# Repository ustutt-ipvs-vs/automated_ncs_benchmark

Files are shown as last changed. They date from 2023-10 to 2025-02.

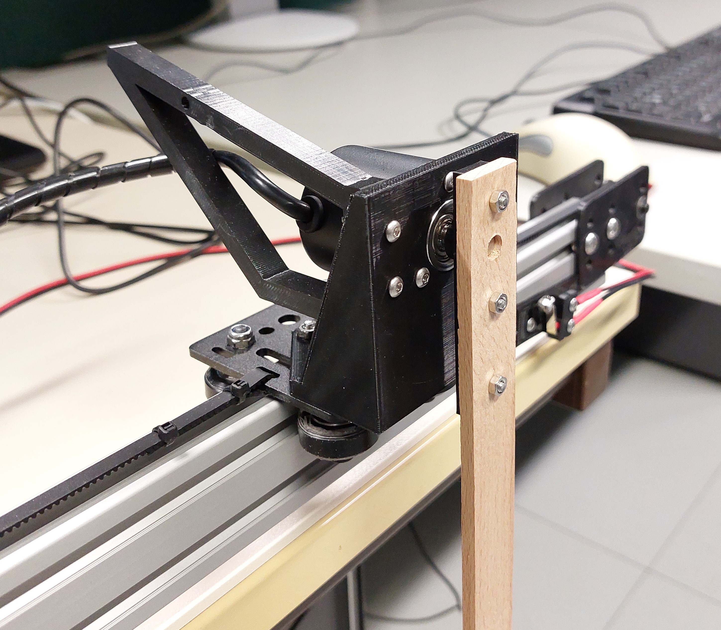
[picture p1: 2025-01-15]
photos/20241224_161821.jpg

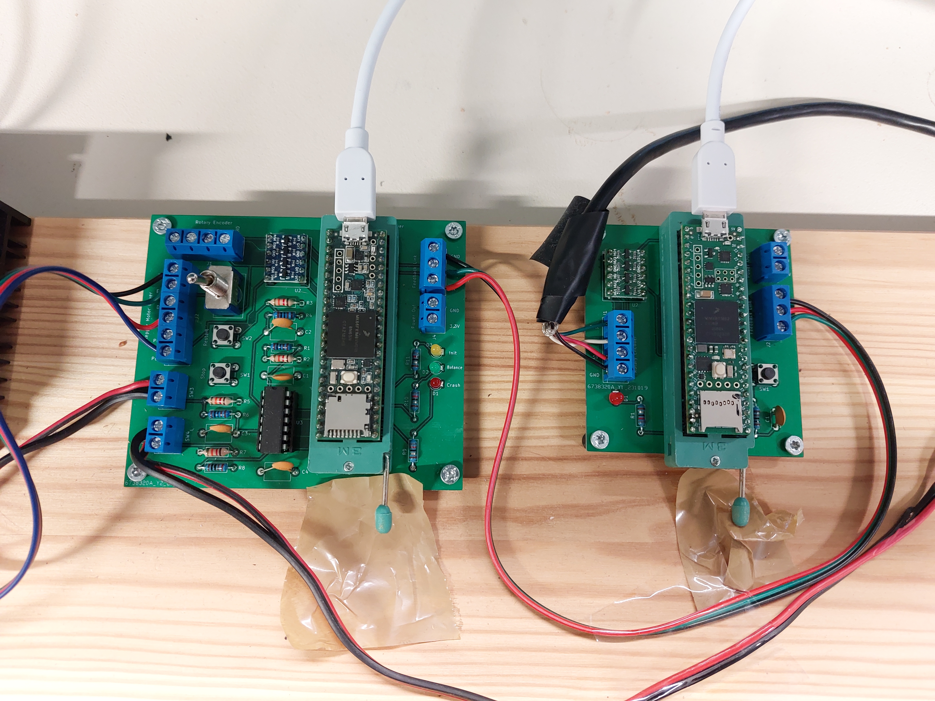
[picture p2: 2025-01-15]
photos/20241224_161937.jpg

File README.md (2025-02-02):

# Automated NCS Benchmark Setup
This repository contains the source code, hardware schematics, 3D printing files, and documentation of the open source benchmark setup described in the paper "Combining Dynamic Deterministic Latency Bounds and Networked Control Systems".

The paper can be found here: https://doi.org/10.1109/IPCCC59868.2024.10850021

The video below shows a demo of an automated evaluation with 15 configurations and re-swing-ups between each configuration.

[Demo Video](https://github.com/ustutt-ipvs-vs/automated_ncs_benchmark/assets/69897594/da2cac4a-8f67-4f81-817d-bd36dadb8c46)

## Overview
This repository is structured as follows:

- `sender-receiver-linux`: Software components for the sender side and receiver side computers
- `sender-receiver-teensy`: Sender and receiver scripts for the Teensy microcontrollers
- `network-config`: Bash scripts to configure the software switch and the endpoints
    - `scheduling-switch-config`: Scripts to configure the Qdisc and queue sizes at the software switch
- `control-approaches-design`: Files containing calculations for the parameters of the various control approaches for the inverted pendulum.
- `PCB-Design`: Design files of the sender and receiver PCB (KiCad)
- `3d-printable-parts`: Design files of the 3D-printed parts that were used for the construction of the inverted pendulum.
- `photos`: Photos of the inverted pendulum

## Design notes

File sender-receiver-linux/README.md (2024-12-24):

# Pendulum Sender and Receiver for Linux
This CMake project contains the code for following programs:
- Sender component for the sensor-side single-board computer
- Receiver component for the actuator-side single-board computer

All the code is written in C++. The following libraries are used:
- `sockpp` to open UDP sockets
- `CppLinuxSerial` to interact with the USB serial interface
- `nlohmann/json` to generate the JSON log files

`sockpp` and `CppLinuxSerial` are shared libraries: They must be installed on the system that is supposed to run the program. They are not included in the executable.
`nlohmann/json` is included in the source code of this project. Thus, the library is included in the executable.

## Preparation
### Installing CMake
Unfortunately, the APT repository only has an outdated version of CMake at the time of writing. Therefore, `sudo apt install cmake` doesn't work.

Instead, install executable from https://cmake.org/download/ .

To use CMake, you need to install `build-essential` too:
```
sudo apt install build-essential
```

### Installing `sockpp`
`sockpp` is a high-level socket library for C++.

```
git clone https://github.com/fpagliughi/sockpp.git
cd sockpp
git checkout f3100f575b38e83a1f2464ca54228bebb1282679
mkdir build
cd build
cmake ..
sudo cmake --build . --target install
```

### Installing `CppLinuxSerial`
`CppLinuxSerial` is a library to access the serial ports in C++.

```
git clone https://github.com/gbmhunter/CppLinuxSerial.git
cd CppLinuxSerial
git checkout ae3c8f7c5e90b3c64e9a3114159923bf45e63e23
mkdir build
cd build
cmake ..
make
sudo make install
```

## Compiling the Source
```
mkdir cmake-build-debug
cd cmake-build-debug
cmake ..
cmake --build .
```

To compile the different targets individually, you can also run instead of the last command:
```
cmake --build . --target pendulum_sender
cmake --build . --target pendulum_receiver
```

## Make Sure Dependencies are Found
You need to make sure that the shared libraries (`sockpp` and `CppLinuxSerial`) can be found. For this purpose, you need to add the path of the libraries (usually `/usr/local/lib`) to the `LD_LIBRARY_PATH` variable:
```
export LD_LIBRARY_PATH=/usr/local/lib:$LD_LIBRARY_PATH
```

## Note About Connecting Teensy via USB
Sometimes, the serial socket doesn't work when the Teensy has been plugged in for a longer time.
In this case, there simply is no input from the serial interface, no errors.

To avoid this problem:
1. Unplug the Teensy
2. Plug in the Teensy
3. Launch the program on the single-board computer immediately (max 10 seconds after plugging in)

## Starting Configurations
The sender and receiver can be started with various parameter options:

### Starting the Sender
#### With single-run config file
````
./pendulum_sender f config_sender_single.json
````

#### With sequence config file
````
./pendulum_sender s config_sender_sequence.json
````

### Starting the Receiver
````
./pendulum_receiver config_receiver.json
````

## Configuration Files
### Sender Config (single run)
```json
{
  "b": 200.0,
  "r": 35.0,
  "numThresholds": 3,
  "thresholds": [0, -200, -400],
  "prioMapping": [0, 1, 2, 7],
  "costs": [1, 1, 1, 0],
  "bias": 0,
  
  /* Option 1: slidingWindow: */
  "sendTriggeringApproach": "slidingWindow",
  "historySize": 100,
  "samplingPeriods": [100, 90, 80, 70, 60, 50, 40, 30, 20, 10],
  "samplingPeriodSensitivityFactor": 1.0,
  "samplingPeriodSensitivityOffset": 0.0,
  
  /* Option 2: simpleThreshold: */
  "sendTriggeringApproach": "simpleThreshold",
  "angleTransmissionThreshold": 1.23,
  
  "initialPriorityClass": 0,
  "serialDeviceName": "auto",
  "receiverAddress": "10.0.1.3",
  "networkDelaysPerPrio": [2, 4, 6, 8, 10, 12, 14, 16]
}
```

with
- `b`: Bucket size of the token bucket
- `r`: Refill rate of the token bucket
- `numThresholds`: Number of thresholds given by the `thresholds` array.
- `thresholds`: Array of thresholds (floating point numbers) for the priority classes. The lowest threhold `- infinity` is ommited from the array.
- `prioMapping`: Array specifying the mapping from the thresholds to the priority classes (integers 0-7).
- `costs`: Array of costs associated with the priority classes. First element associated with best priority class.
- `bias` Bias as an integer value. Is *added* to the raw sensor value before sending it to the receiver. Default value: `0`
- `sendTriggeringApproach`: String. Determines the approach to trigger the sending of a new sensor value. Default: `slidingWindow`. Possible options:
    - `slidingWindow`: Uses a sliding window to determine the maximum absolute angle change. The sampling period is determined by the maximum absolute angle change.
      For this approach, the following parameters are required: `historySize`, `samplingPeriods`, `samplingPeriodSensitivityFactor`, `samplingPeriodSensitivityOffset`.
    - `simpleThreshold`: Uses a simple threshold. Whenever the absolute angle value exceeds the threshold, a new sensor value is sent.
        For this approach, the following parameter is required: `angleTransmissionThreshold`.
- `historySize`: Number of samples kept in the sensor history to determine the maximum absolute angle change.
- `samplingPeriods`: Array of 10 sampling periods in milliseconds, where the first element corresponds to the smallest change and the 10th element corresponds to the largest maximum absolute angle change.
- `initialPriorityClass`: Priority class used at start ()
- `samplingPeriodSensitivityFactor`: Factor by which the maximum absolute angle change is multiplied to determine sampling period. Default value: `1.0`
- `samplingPeriodSensitivityOffset`: Offset by which the maximum absolute angle change is shifted to determine sampling period. Default value: `0.0`
- `serialDeviceName`: Linux file which associated with the serial interface of the sender Teensy. If you set it to `auto`, the computer tries to recognize a Teensy device automatically. Default value: `auto`
- `receiverAddress`: IP address of the receiver PC
- `networkDelaysPerPrio`: Array of network delays in milliseconds (integers) for each priority class. Must have 8 elements. First element associated with the best priority class (0).

### Sender Config (multiple MPTB configurations)
This config allows to run multiple MPTB configurations one after another without manual interaction.
```json
{
  "mptbSequence": [
    {
      "name": "mptb1",
      "durationMinutes": 1.0,
      "b": 200.0,
      "r": 35.0,
      "numThresholds": 3,
      "thresholds": [-20000000, -200, -400],
      "prioMapping": [0, 1, 2, 7],
      "costs": [1, 1, 1, 0]
    },
    {
      "name": "mptb2",
      "durationMinutes": 0.5,
      "b": 5000.0,
      "r": 350.0,
      "numThresholds": 2,
      "thresholds": [-20000, -40000],
      "prioMapping": [0, 1, 2],
      "costs": [2, 1, 0]
    }
  ],

  /* Option 1: slidingWindow: */
  "sendTriggeringApproach": "slidingWindow",
  "historySize": 100,
  "samplingPeriods": [100, 90, 80, 70, 60, 50, 40, 30, 20, 10],
  "samplingPeriodSensitivityFactor": 1.0,
  "samplingPeriodSensitivityOffset": 0.0,

  /* Option 2: simpleThreshold: */
  "sendTriggeringApproach": "simpleThreshold",
  "angleTransmissionThreshold": 1.23,
  
  "bias": 0,
  "serialDeviceName": "auto",
  "receiverAddress": "10.0.1.5",
  "networkDelaysPerPrio": [2, 4, 6, 8, 10, 12, 14, 16]
}

```

with
- `name`: Name of the configuration. This name is used for the file name of the log file.
- `mptbSequence`: Array with an arbitrary number of MPTB configuration objects. These configurations are executed sequentially in the order given by the array.
- `durationMinutes`: Number of minutes (floating point number) that this configuration should be executed.
- All other parameters like in the single-run config.

### Receiver Config
```json
{
  "receiverAddress": "10.0.1.3",
  "pendulumType": "oldPendulum",
  "serialDeviceName": "auto",
  "swingUpBehavior": "crashAndSwingUpAtNewConfig",
  "sailType": "sail14",
  "controllerKVector": [1.0, 2.0, 3.0, 4.0],
  "controllerIntegratorParam": 1.0,
  "controlApproach":"mLQR"
}
```

with 
- `receiverAddress`: IP address of the receiver PC (i.e., own IP address). This IP address is used to bind the UDP socket.
- `pendulumType`: Type of the pendulum. Influences the motor characteristics. Possible options:
    - `oldPendulum`: The pendulum constructed by Ben Carabelli
    - `newPendulum`: The two pendulums constructed by David Augustat
- `serialDeviceName`: Linux file which associated with the serial interface of the receiver Teensy. If you set it to `auto`, the computer tries to recognize a Teensy device automatically. Default value: `auto`
- `swingUpBehavior`: Determines if and when the pendulum should swing up itself. Default: `noSwingUp`. Possible options:
    - `swingUpAtStart`: Only swings up the pendulum at the start. If the pendulum crashes, it will stay crashed.
    - `swingUpAtNewConfigIfCrashed`: Swings up the pendulum at start and at the beginning of each new config, **if the pendulum has crashed before**. If the pendulum is already balancing at the start of a new config, it will not swing up.
    - `crashAndSwingUpAtNewConfig`: Swings up the pendulum at the start. At the beginning of each new config, the pendulum intenionally stops balancing to enforce a crash. Then the pendulum swings up again.
    - `noSwingUp`: Manual mode where the pendulum must be held upwards by the operating person at the beginning. No swing-up.
- `sailType`: Determines which sail is used. Default: `noSail`. Possible options:
    - `noSail`: No sail is used.
    - `sail10`
    - `sail14`
    - `sail17`
    - `sail20`
- `controllerKVector`: Vector of 4 floating point numbers. The RobustIO controller uses this vector as the K vector. Default: `[3.6723, 13.5022, -74.6153, -19.8637]`
- `controllerIntegratorParam`: Floating point number. The RobustIO controller uses this value as the integrator parameter. Default: `5.0322`
- `controlApproach`: String. Determines which control approach is used. Default: `mLQR`. Possible options:
    - `mLQR`
    - `RobustIO`

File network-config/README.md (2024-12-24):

# Network Configuration Scripts for VLANs:

## Scripts:
Run the scripts on the devices respectively to set up the correct network config.

`configure-switch.sh` does the following
- Sets up VLANs on `enp1s0f0`, `enp1s0f1` `enp1s0f2` and `enp1s0f3` with VLAN ID `100`. For this purpose, the VLAN interfaces `enp1s0f0.100`, `enp1s0f1.100`, `enp1s0f2.100` and `enp1s0f3.100` get created.
- Creates a virtual bridge between `enp1s0f0.100`, `enp1s0f1.100`, `enp1s0f2.100` and `enp1s0f3.100`.
- Assigns the IP address to the switch PC.

All other `configure-*.sh` scripts set up a VLAN interface set up VLANs as `eth0.100` or `enp0s25.100` interfaces with VLAN ID 100 and assign an IP address.

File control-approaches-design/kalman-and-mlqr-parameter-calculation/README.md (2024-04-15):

# How to use
Make sure that the [Julia programming language](https://julialang.org/) is installed on your machine.

Then run from this directory:
```
julia demonstrator-multi-period.jl
```

The script creates a header file 
```
../sender-receiver-teensy/pendulum_receiver1/KalmanAndMLQRParameters.h
```
with the parameters for the Kalman filter and the mLQR controller.

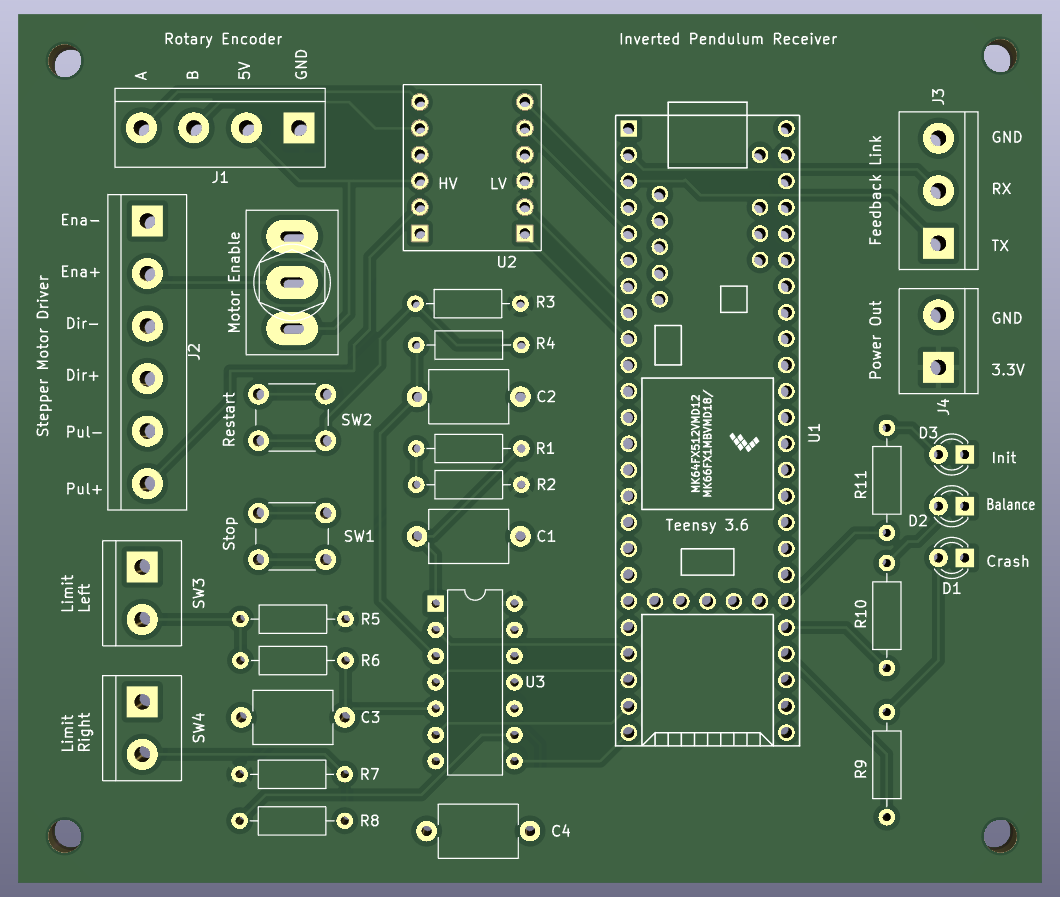
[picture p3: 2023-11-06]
PCB-Design/PCB-Images/receiver-front_06-10-2023.png

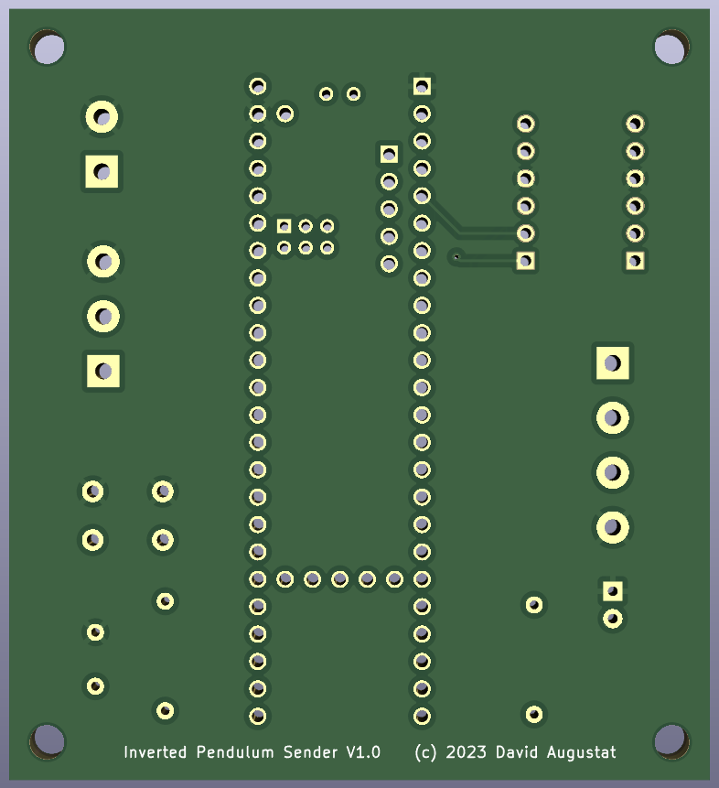
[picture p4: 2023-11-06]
PCB-Design/PCB-Images/sender-back_06-10-2023.png

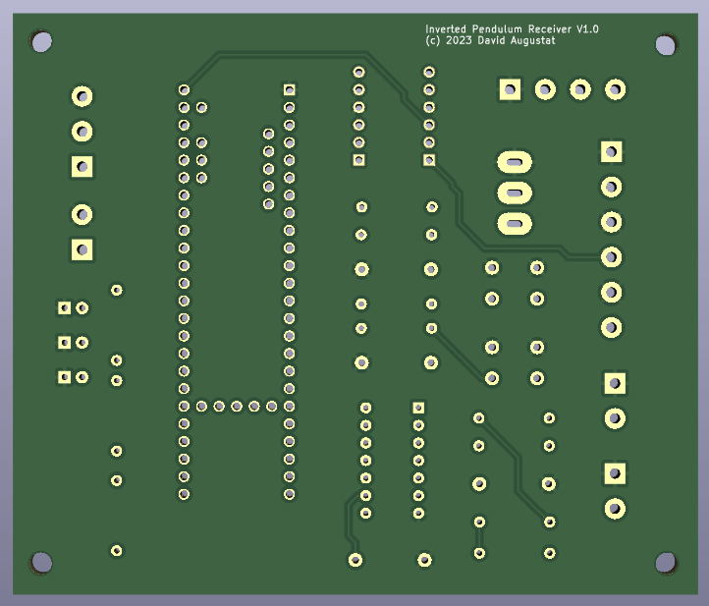
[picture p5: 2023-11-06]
PCB-Design/PCB-Images/receiver-back_06-10-2023.png

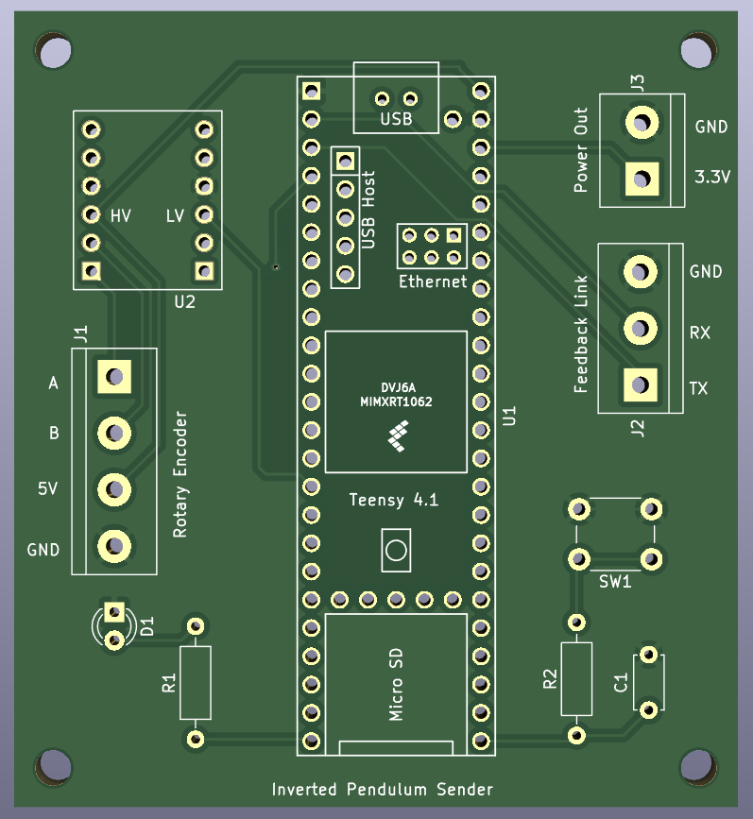
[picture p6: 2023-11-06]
PCB-Design/PCB-Images/sender-front_06-10-2023.png

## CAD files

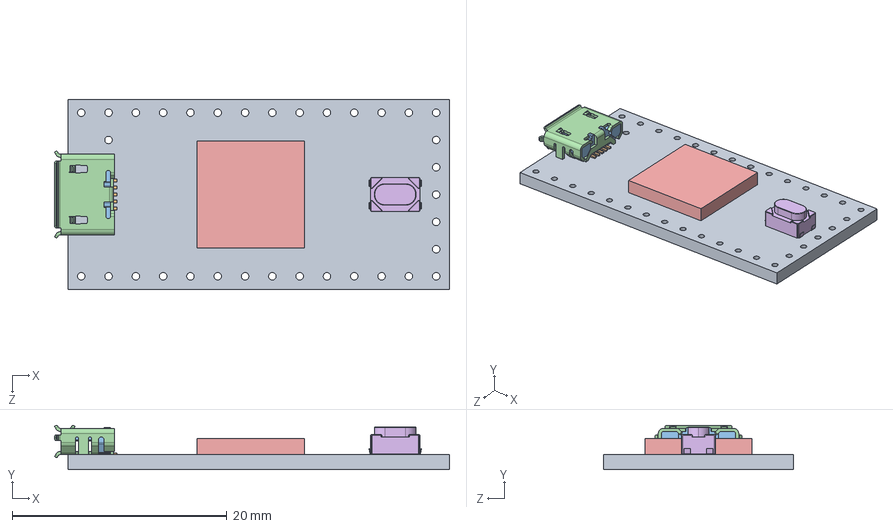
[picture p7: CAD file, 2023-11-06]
PCB-Design/Symbols/teensy.pretty-master/Teensy_4.0_Assembly.STEP
36.8 x 4.12 x 17.7 mm
Teensy_4.0_PCB
Micro USB-B Female 5Pin SMD
NXP iMXRT1062
SKRPACE010 v4

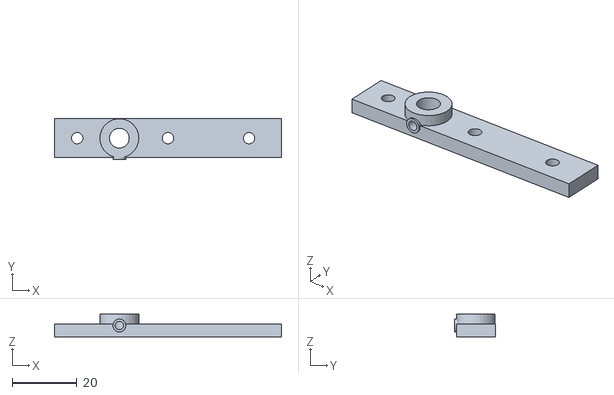
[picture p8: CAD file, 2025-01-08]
3d-printable-parts/rod_attachment.stl
70.0 x 12.5 x 7.00

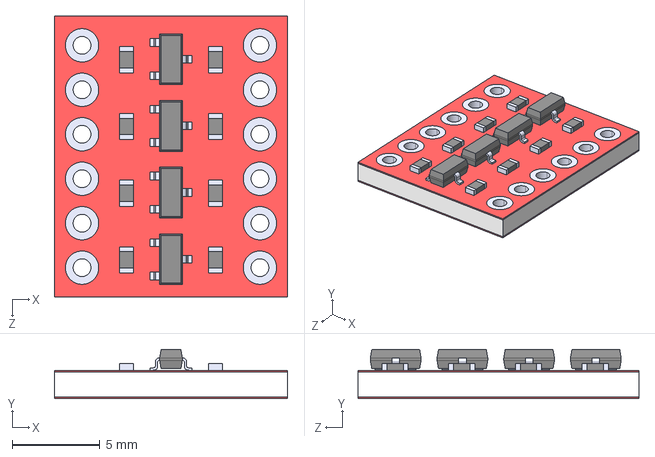
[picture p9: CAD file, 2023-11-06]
PCB-Design/Symbols/BOB-12009/BOB-12009.step
13.3 x 2.80 x 16.1 mm

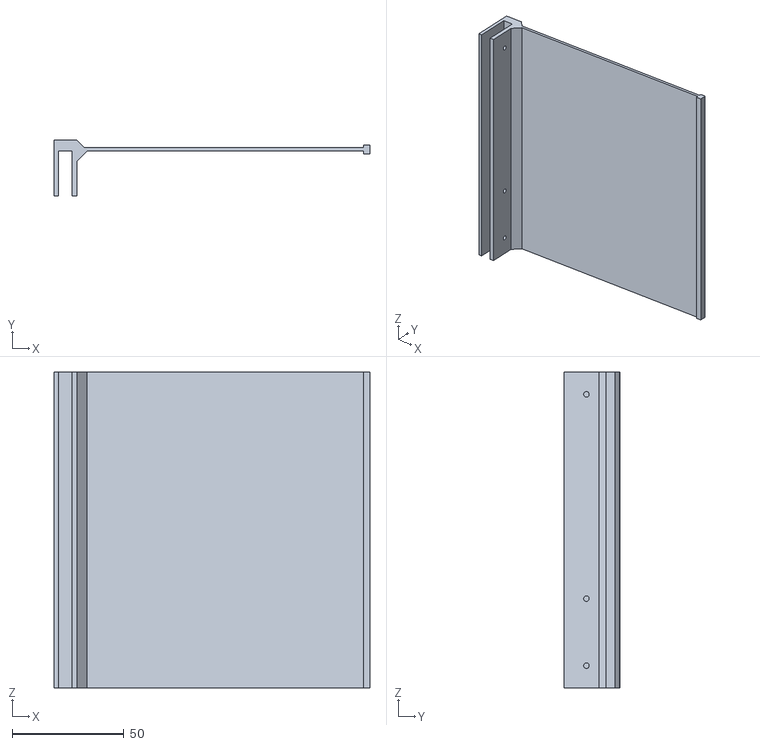
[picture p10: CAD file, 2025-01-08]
3d-printable-parts/sail_14x14.stl
141.4 x 25.0 x 141.4

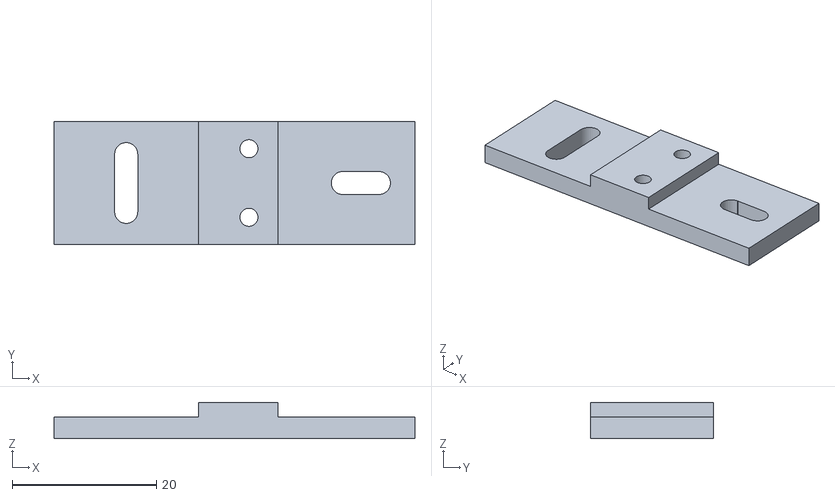
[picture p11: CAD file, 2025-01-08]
3d-printable-parts/endstop_mount.stl
50.0 x 17.0 x 5.00

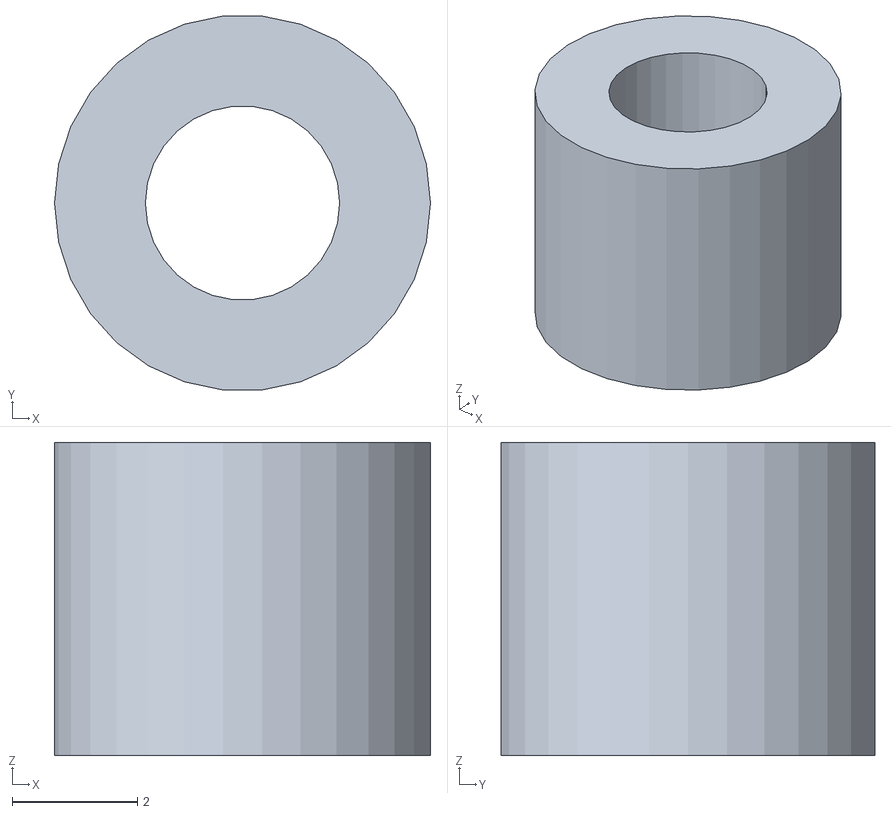
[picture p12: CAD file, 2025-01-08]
3d-printable-parts/pcb_distance.stl
6.00 x 5.97 x 5.00

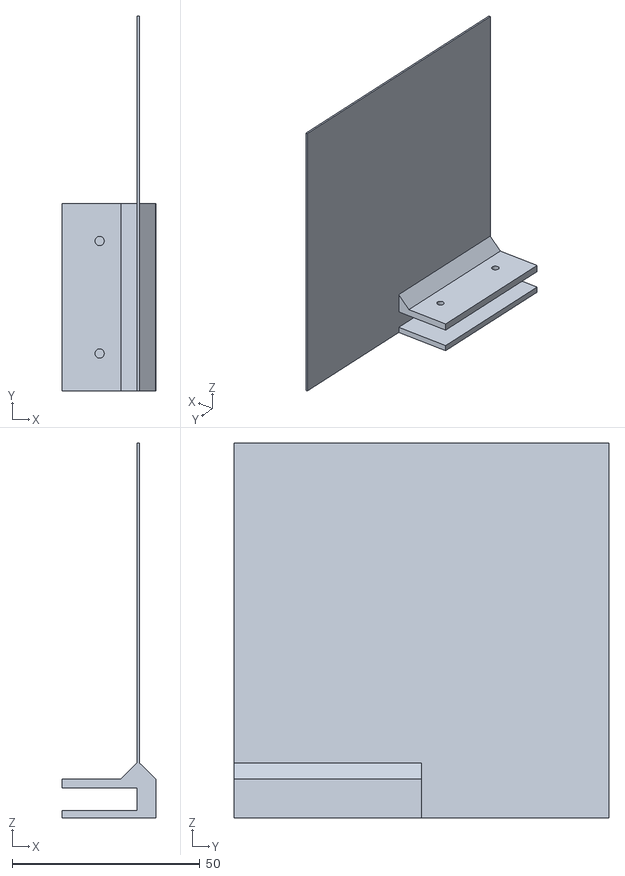
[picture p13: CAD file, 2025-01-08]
3d-printable-parts/sail_10x10.stl
25.0 x 100.0 x 100.0

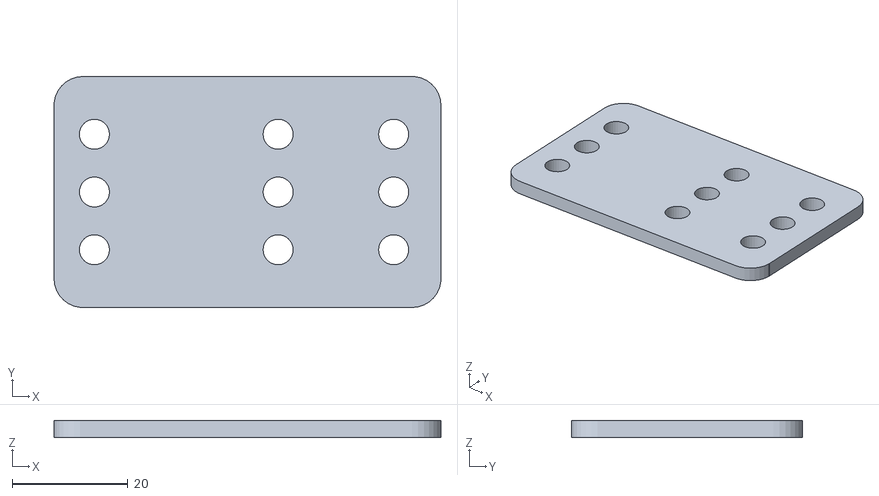
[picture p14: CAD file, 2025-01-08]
3d-printable-parts/idler_mount.stl
67.0 x 40.0 x 3.00

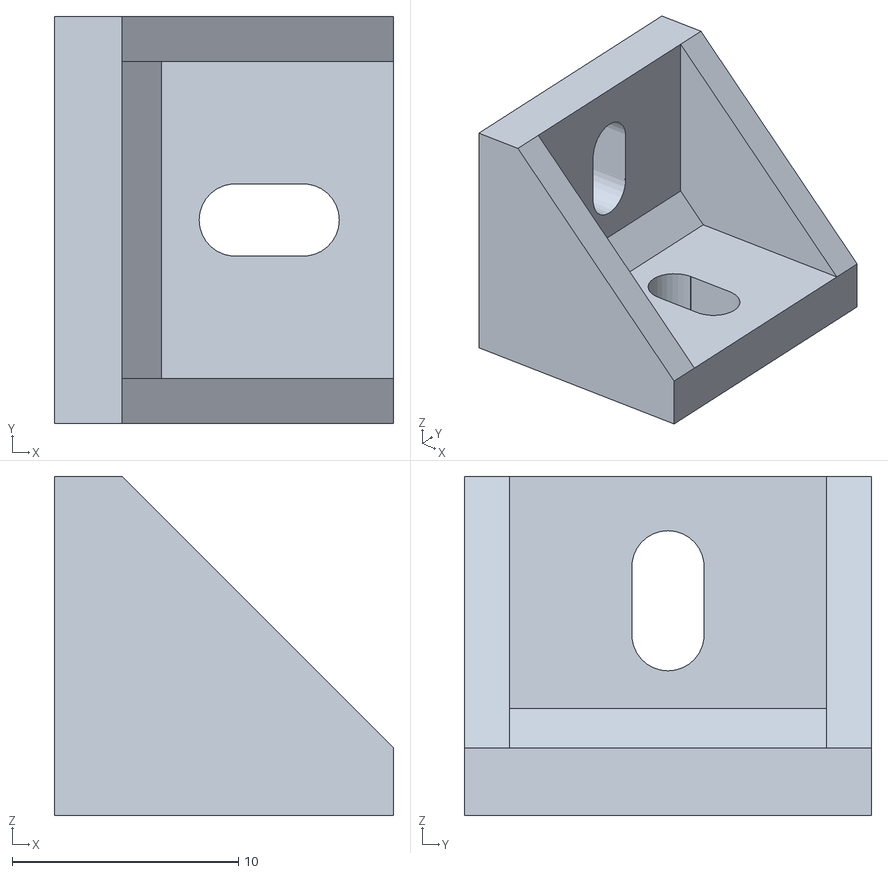
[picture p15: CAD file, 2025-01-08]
3d-printable-parts/corner_profile_mount.stl
15.0 x 18.0 x 15.0

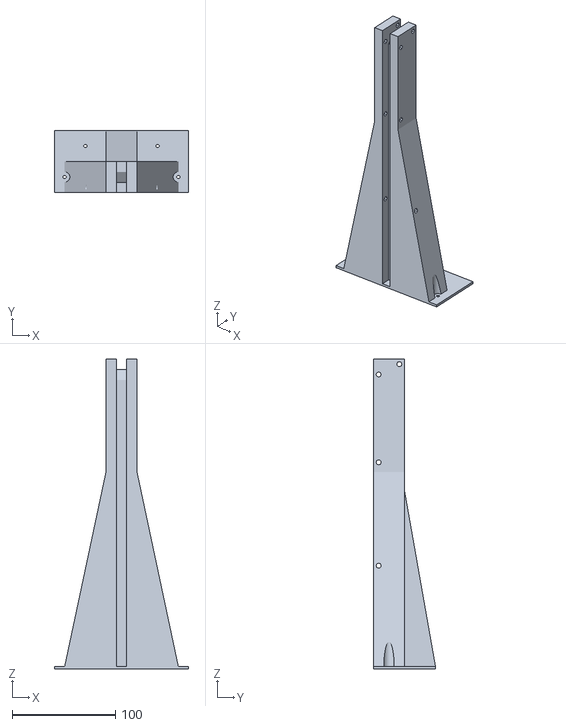
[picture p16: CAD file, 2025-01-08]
3d-printable-parts/cable_tower.stl
130.0 x 60.0 x 300.0

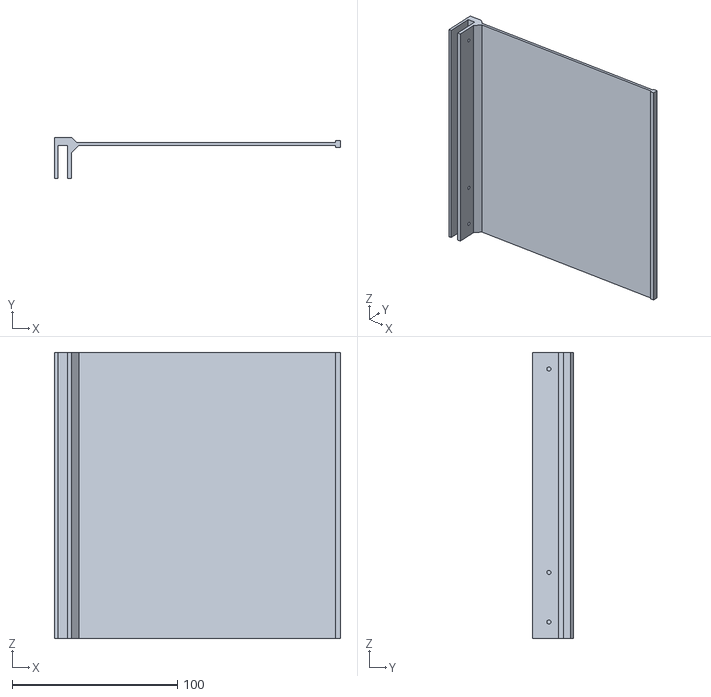
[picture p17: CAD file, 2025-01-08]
3d-printable-parts/sail_17x17.stl
173.2 x 25.0 x 173.2

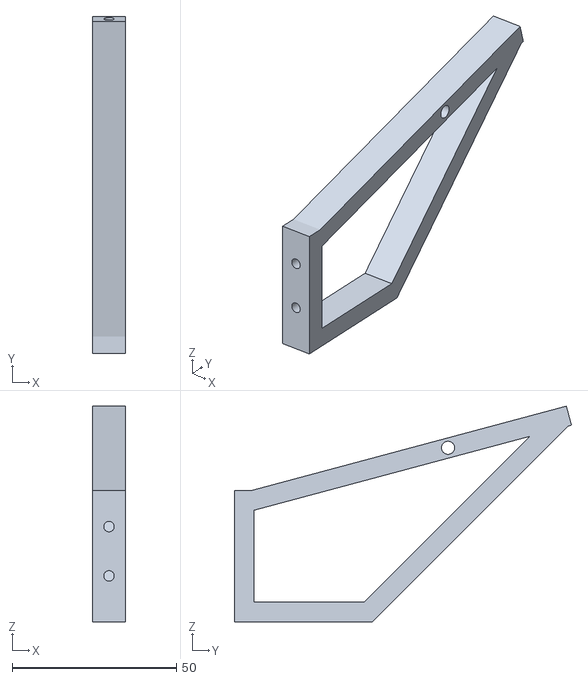
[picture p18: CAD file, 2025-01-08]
3d-printable-parts/sensor_mount_cable_guide.stl
10.0 x 102.6 x 65.7

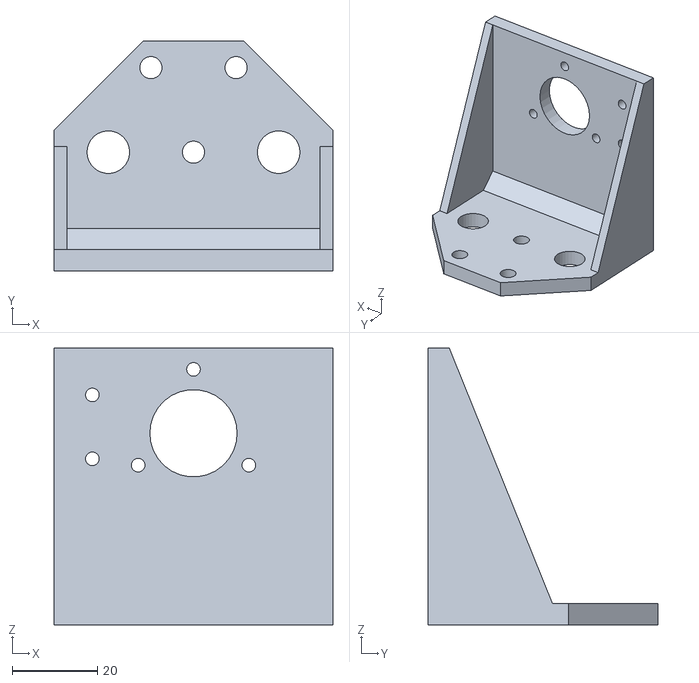
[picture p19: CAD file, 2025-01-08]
3d-printable-parts/sensor_mount.stl
65.5 x 54.0 x 65.0

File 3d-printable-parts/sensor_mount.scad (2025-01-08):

$fn=30;

width=39+15;
length=65.5;
height=65;
screw_d=3.2;

sensor_mount();
translate([4,6,height-6]) sensor_cable_guide();


module sensor_cable_guide(){
    guide_length = 100; // Changing this value is not fully supported
    difference(){
        union(){
            translate([0,6,0]) rotate([15,0,0]) cube([10,guide_length,6]);
            translate([0,0,-34]) cube([10,6,40]);
            translate([0,0,-34]) cube([10,guide_length-64+6,6]);
            translate([0,6+guide_length-64,-34]) rotate([45,0,0]) cube([10,85,6]);
        }
        
        // Screwholes + nuts
        translate([5,-0.1,-20]) rotate([-90,0,0]) cylinder(h=10,d=screw_d);
        translate([5,4,-20]) rotate([-90,0,0]) cylinder(h = 4, r=3.2, $fn=6);
        translate([5,-0.1,-5]) rotate([-90,0,0]) cylinder(h=10,d=screw_d);
        translate([5,4,-5]) rotate([-90,0,0]) cylinder(h = 4, r=3.2, $fn=6); 
    
        
        // Filament hole
        translate([5,70,20]) rotate([-75,0,0]) cylinder(h=50,d=3.2);
        
        // Ziptie hole
        translate([-0.1,65,19.]) rotate([0,90,0]) cylinder(h=12,d=4);
           
    }
    
}
module sensor_mount(){
    difference(){
        union(){
            cube([length,width,5]);
            cube([length,5,height]);
            
            translate([0,10,5]) rotate([135,0,0]) cube([length,10,4]);
            
            // Stability sides
            translate([0,5,height]) rotate([22-180,0,0]) cube([3,25,height+10]);
            translate([length-3,5,height]) rotate([22-180,0,0]) cube([3,25,height+10]);
        }
    
        // Sensor Hole
        translate([length/2,-0.1,45]) rotate([-90,0,0]) cylinder(h=10,d=20.5);
        
        // Sensor Screw holes
        translate([length/2,-0.1,45+15]) rotate([-90,0,0]) cylinder(h=10,d=3.2);
        translate([length/2+12.99,-0.1,45-7.5]) rotate([-90,0,0]) cylinder(h=10,d=3.2);
        translate([length/2-12.99,-0.1,45-7.5]) rotate([-90,0,0]) cylinder(h=10,d=3.2);
        
        // Cable guide holes
        translate([9,-0.1,39]) rotate([-90,0,0]) cylinder(h=10,d=3.2);
        translate([9,-0.1,39+15]) rotate([-90,0,0]) cylinder(h=10,d=3.2);
        
    
        translate([0,15,0]){
        // Screwholes bottom
        translate([32.75,12.9,-0.1]) cylinder(h=10,d=5.2);
        translate([22.75,32.75,-0.1]) cylinder(h=10,d=5.2);      
        translate([42.75,32.75,-0.1]) cylinder(h=10,d=5.2);
        
        // Screwheads bottom
        translate([32.75,12.9,5]) cylinder(h=10,d=11);

        // Wheel Nut openings
        translate([12.75,12.9,-0.1]) cylinder(h=10,d=10);
        translate([length-12.75,12.9,-0.1]) cylinder(h=10,d=10);
            
        // 45° Cut bottom
        translate([0,18,-0.1]) rotate([0,0,45]) cube([30,20,6]);
        translate([length,18,-0.1]) rotate([0,0,45]) cube([20,30,6]);
            
        }

        
        //bottom and back cut
        translate([-0.1,-0.1,-length]) cube([length+1,width+1,length]);
        translate([-0.1,-length,-length]) cube([length+1,length,2*length]);
    
    }  
}

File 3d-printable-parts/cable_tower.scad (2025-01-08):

height=300;
plate_thick = 2.5;
screw_d=3.2;

cable_tower();


module cable_tower(){
    difference(){
        union(){
            cube([30,30,height]);
            translate([-10,0,0]) cube([50,30,50]);
            translate([-50,0,0]) cube([130,60,plate_thick]);
            
            translate([-40,0,plate_thick]) rotate([0,12,0]) cube([30,30,195]);
            translate([40+30,30,plate_thick]) rotate([0,12,180]) cube([30,30,195]);
            translate([0,60,plate_thick]) rotate([0,10,270]) cube([30,30,175]);
                      
        }
    
    // Bottom cut
    translate([-50,-10,-20]) cube([130,80,20]);
        
    // Cable channel
    translate([10,-0.1,plate_thick]) cube([10,10,height]);
    translate([10,0,height-10]) cube([10,31,11]);
    translate([10,0,height-30]) rotate([45,0,0]) cube([10,31,11]);
        
    // Ziptie holes
    translate([-10,5,height-15]) rotate([0,90,0]) cylinder(h=50,d=5);
    translate([-10,25,height-5]) rotate([0,90,0]) cylinder(h=50,d=5);
    translate([-10,5,height-100]) rotate([0,90,0]) cylinder(h=50,d=5);
    translate([-100,5,height-200]) rotate([0,90,0]) cylinder(h=200,d=5);
    
    // Screwholes bottom
    translate([-40,15,-0.1]) cylinder(h=5, d=screw_d, $fn=30);
    translate([70,15,-0.1]) cylinder(h=5, d=screw_d, $fn=30);
    translate([-40,15,plate_thick]) cylinder(h=25, d=10, $fn=30);
    translate([70,15,plate_thick]) cylinder(h=25, d=10, $fn=30);
    
    translate([-20,45,-0.1]) cylinder(h=5, d=screw_d, $fn=30);
    translate([50,45,-0.1]) cylinder(h=5, d=screw_d, $fn=30);
    
        
    
    }  
}

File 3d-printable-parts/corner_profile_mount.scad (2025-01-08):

width=18;
length=15;
screw_d=3.2;

corner();


module corner(){
    difference(){
        union(){
            cube([length,width,3]);
            cube([3,width,length]);
            
            translate([0,0,3.5]) rotate([0,45,0]) cube([4,width,3]);
            translate([3,0,length]) rotate([0,135,0]) cube([length-3,2,sqrt(2*(length-3)*(length-3))]);
            translate([3,width-2,length]) rotate([0,135,0]) cube([length-3,2,sqrt(2*(length-3)*(length-3))]);
        }
    
    
    // Screwholes bottom
    translate([length-7,width/2-screw_d/2,-0.1]) cube([3,screw_d,5]);
    translate([length-7,width/2,-0.1]) cylinder(h=5, d=screw_d, $fn=30);
    translate([length-4,width/2,-0.1]) cylinder(h=5, d=screw_d, $fn=30);
    
    // Screwholes side
    translate([-0.1,width/2-screw_d/2,length-7]) cube([5,screw_d,3]);
    translate([-0.1,width/2,length-7]) rotate([0,90,0]) cylinder(h=5, d=screw_d, $fn=30);
    translate([-0.1,width/2,length-4]) rotate([0,90,0]) cylinder(h=5, d=screw_d, $fn=30);
        
    //bottom and back cut
    translate([-0.1,-0.1,-length]) cube([length,width+1,length]);
    translate([-length,-0.1,-0.1]) cube([length,width+1,length+1]);
    
    }  
}

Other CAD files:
3d-printable-parts/endstop_mount.scad
3d-printable-parts/idler_mount.scad
3d-printable-parts/pcb_distance.scad
3d-printable-parts/rod_attachment.scad
3d-printable-parts/sail.scad

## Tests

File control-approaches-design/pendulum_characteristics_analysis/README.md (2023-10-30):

# How To

1. Upload the `teensy_encoder_serial_readout.ino` sketch onto a Teensy microcontroller that is connected to a rotary encoder on pin 2 an 3.
2. Plug in the Teensy in the computer. The teensy immediately starts writing the raw encoder values to the Serial interface every millisecond.
3. Run the `teensy_encoder_log.sh` script to receive the values from the serial interface and write them to a log file.
4. Do your measurements.
5. Stop the script with `Ctrl+C` when you are done measuring.
6. Use the `analyze_trace.py` script to analyze the created log file.

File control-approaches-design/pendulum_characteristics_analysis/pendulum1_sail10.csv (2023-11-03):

timeMicros | encoderValue
467001 | 0
468001 | 0
469001 | 0
470001 | 0
1099000 | 0
1100000 | 0
1101000 | 0
1102000 | 0
1103000 | 0
1104000 | 0
1105000 | 0
1106000 | 0
1107000 | 0
1108000 | 0
1109000 | 0
1110000 | 0
1111000 | 0
1112000 | 0
1113000 | 0
1114000 | 0
1115000 | 0
1116000 | 0
1117000 | 0
1118000 | 0
1119000 | 0
1120000 | 0
1121000 | 0
1122000 | 0
1123000 | 0
1124000 | 0
1125000 | 0
1126000 | 0
1127000 | 0
1128000 | 0
1129000 | 0
1130000 | 0
1131000 | 0
1132000 | 0
1133000 | 0
1134000 | 0
1135000 | 0
1136000 | 0
1137000 | 0
1138000 | 0
1139000 | 0
1140000 | 0
1141000 | 0
1142000 | 0
1143000 | 0
1144000 | 0
1145000 | 0
1146000 | 0
1147000 | 0
1148000 | 0
1149000 | 0
1150000 | 0
1151000 | 0
1152000 | 0
1153000 | 0
1154000 | 0
1155000 | 0
1156000 | 0
1157000 | 0
1158000 | 0
1159000 | 0
1160000 | 0
1161000 | 0
1162000 | 0
1163000 | 0
1164000 | 0
1165000 | 0
1166000 | 0
1167000 | 0
1168000 | 0
1169000 | 0
1170000 | 0
1171000 | 0
1172000 | 0
1173000 | 0
1174000 | 0
1175000 | 0
1176000 | 0
1177000 | 0
1178000 | 0
1179000 | 0
1180000 | 0
1181000 | 0
1182000 | 0
1183000 | 0
1184000 | 0
1185000 | 0
1186000 | 0
1187000 | 0
1188000 | 0
1189000 | 0
1190000 | 0
1191000 | 0
1192000 | 0
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

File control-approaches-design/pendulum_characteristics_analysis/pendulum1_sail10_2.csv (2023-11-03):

timeMicros | encoderValue
508001 | 0
509001 | 0
510001 | 0
511001 | 0
956002 | 0
957002 | 0
958002 | 0
959002 | 0
960002 | 0
961002 | 0
962002 | 0
963002 | 0
964002 | 0
965002 | 0
966002 | 0
967002 | 0
968002 | 0
969002 | 0
970002 | 0
971002 | 0
972002 | 0
973002 | 0
974002 | 0
975002 | 0
976002 | 0
977002 | 0
978002 | 0
979002 | 0
980002 | 0
981002 | 0
982002 | 0
983002 | 0
984002 | 0
985002 | 0
986002 | 0
987002 | 0
988002 | 0
989002 | 0
990002 | 0
991002 | 0
992002 | 0
993002 | 0
994002 | 0
995002 | 0
996002 | 0
997002 | 0
998002 | 0
999002 | 0
1000002 | 0
1001002 | 0
1002002 | 0
1003002 | 0
1004002 | 0
1005002 | 0
1006002 | 0
1007002 | 0
1008002 | 0
1009002 | 0
1010002 | 0
1011002 | 0
1012002 | 0
1013002 | 0
1014002 | 0
1015002 | 0
1016002 | 0
1017002 | 0
1018002 | 0
1019002 | 0
1020002 | 0
1021002 | 0
1022002 | 0
1023002 | 0
1024002 | 0
1025002 | 0
1026002 | 0
1027002 | 0
1028002 | 0
1029002 | 0
1030002 | 0
1031002 | 0
1032002 | 0
1033002 | 0
1034002 | 0
1035002 | 0
1036002 | 0
1037002 | 0
1038002 | 0
1039002 | 0
1040002 | 0
1041002 | 0
1042002 | 0
1043002 | 0
1044002 | 0
1045002 | 0
1046002 | 0
1047002 | 0
1048002 | 0
1049002 | 0
1050002 | 0
1051002 | 0
1052002 | 0
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

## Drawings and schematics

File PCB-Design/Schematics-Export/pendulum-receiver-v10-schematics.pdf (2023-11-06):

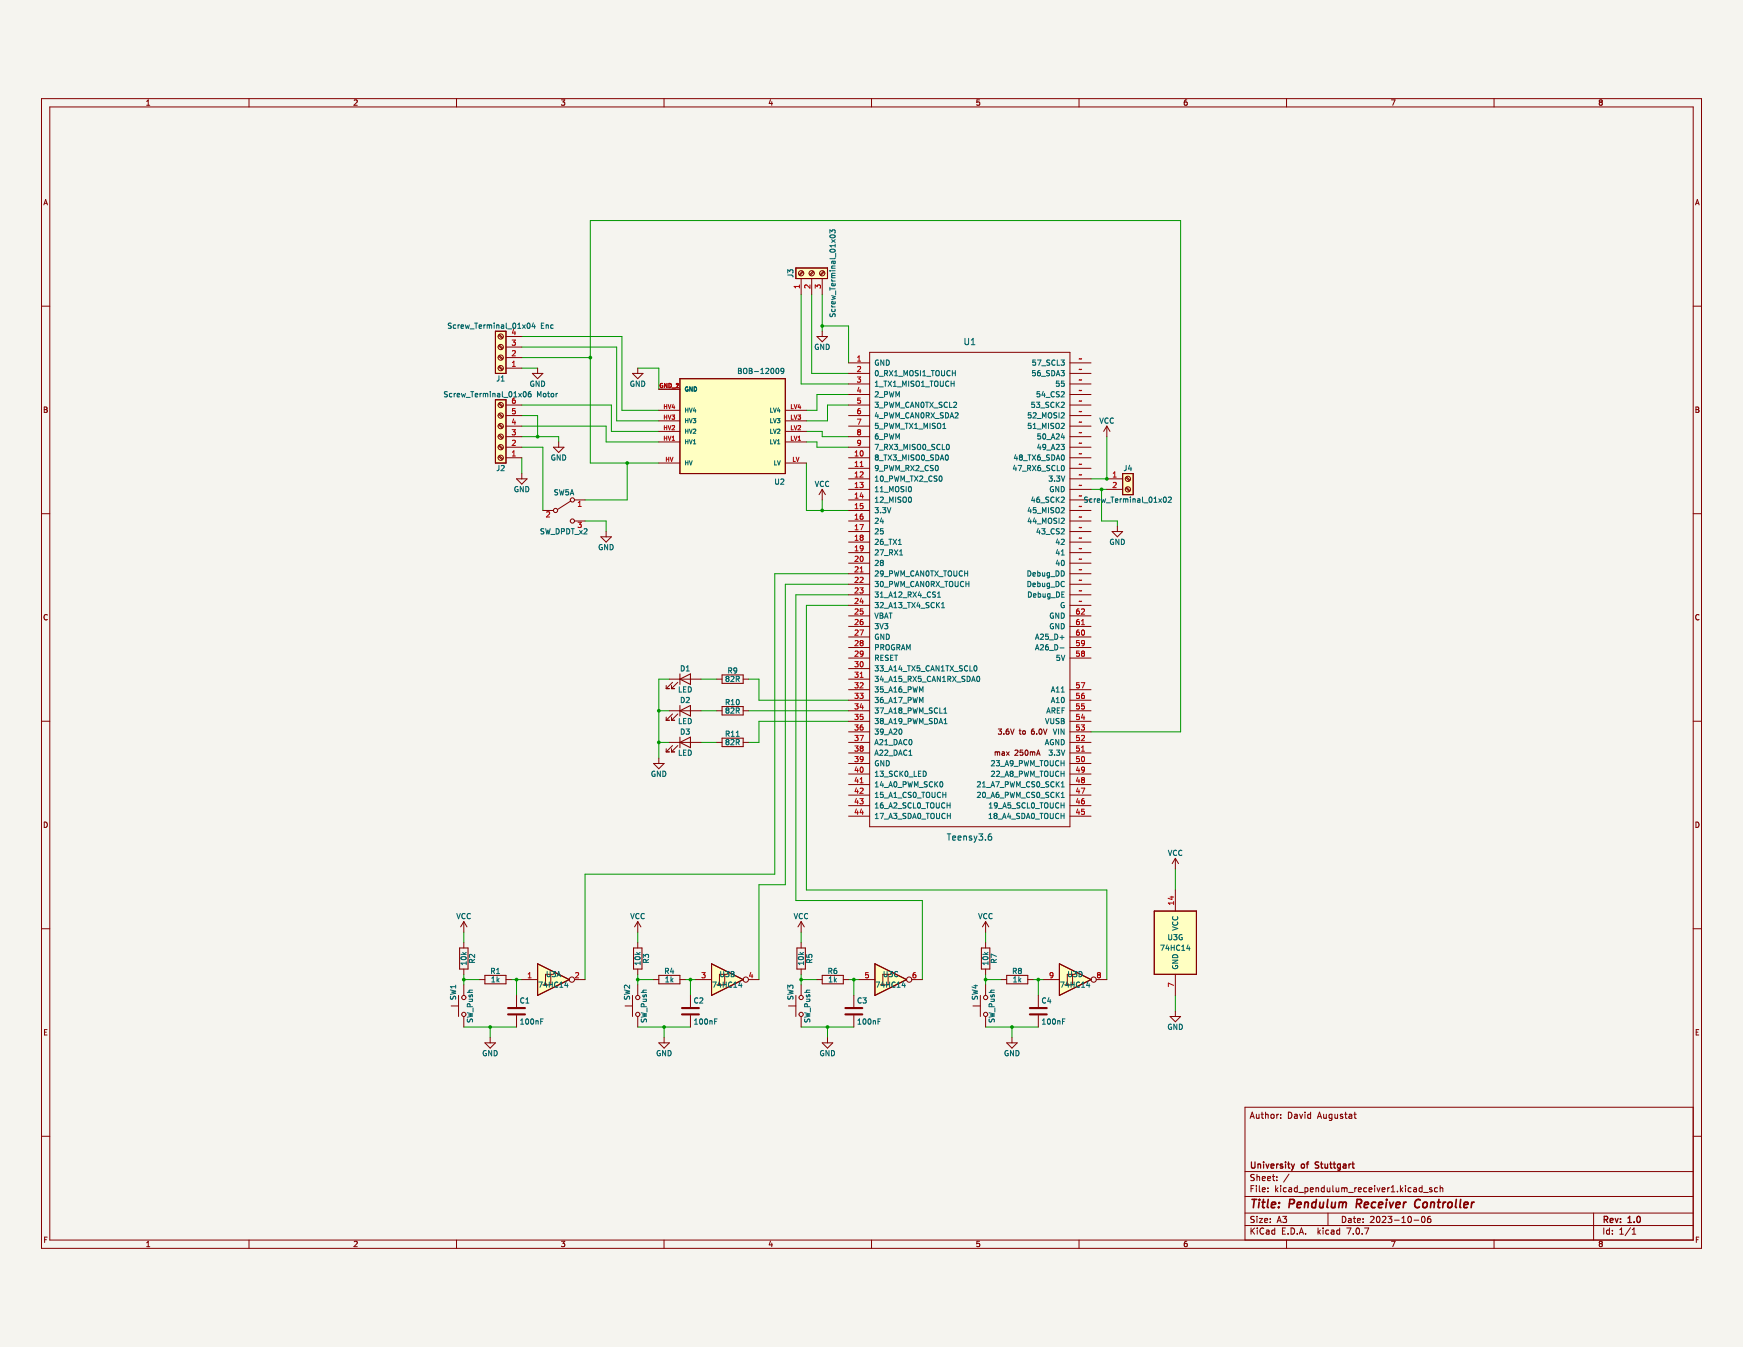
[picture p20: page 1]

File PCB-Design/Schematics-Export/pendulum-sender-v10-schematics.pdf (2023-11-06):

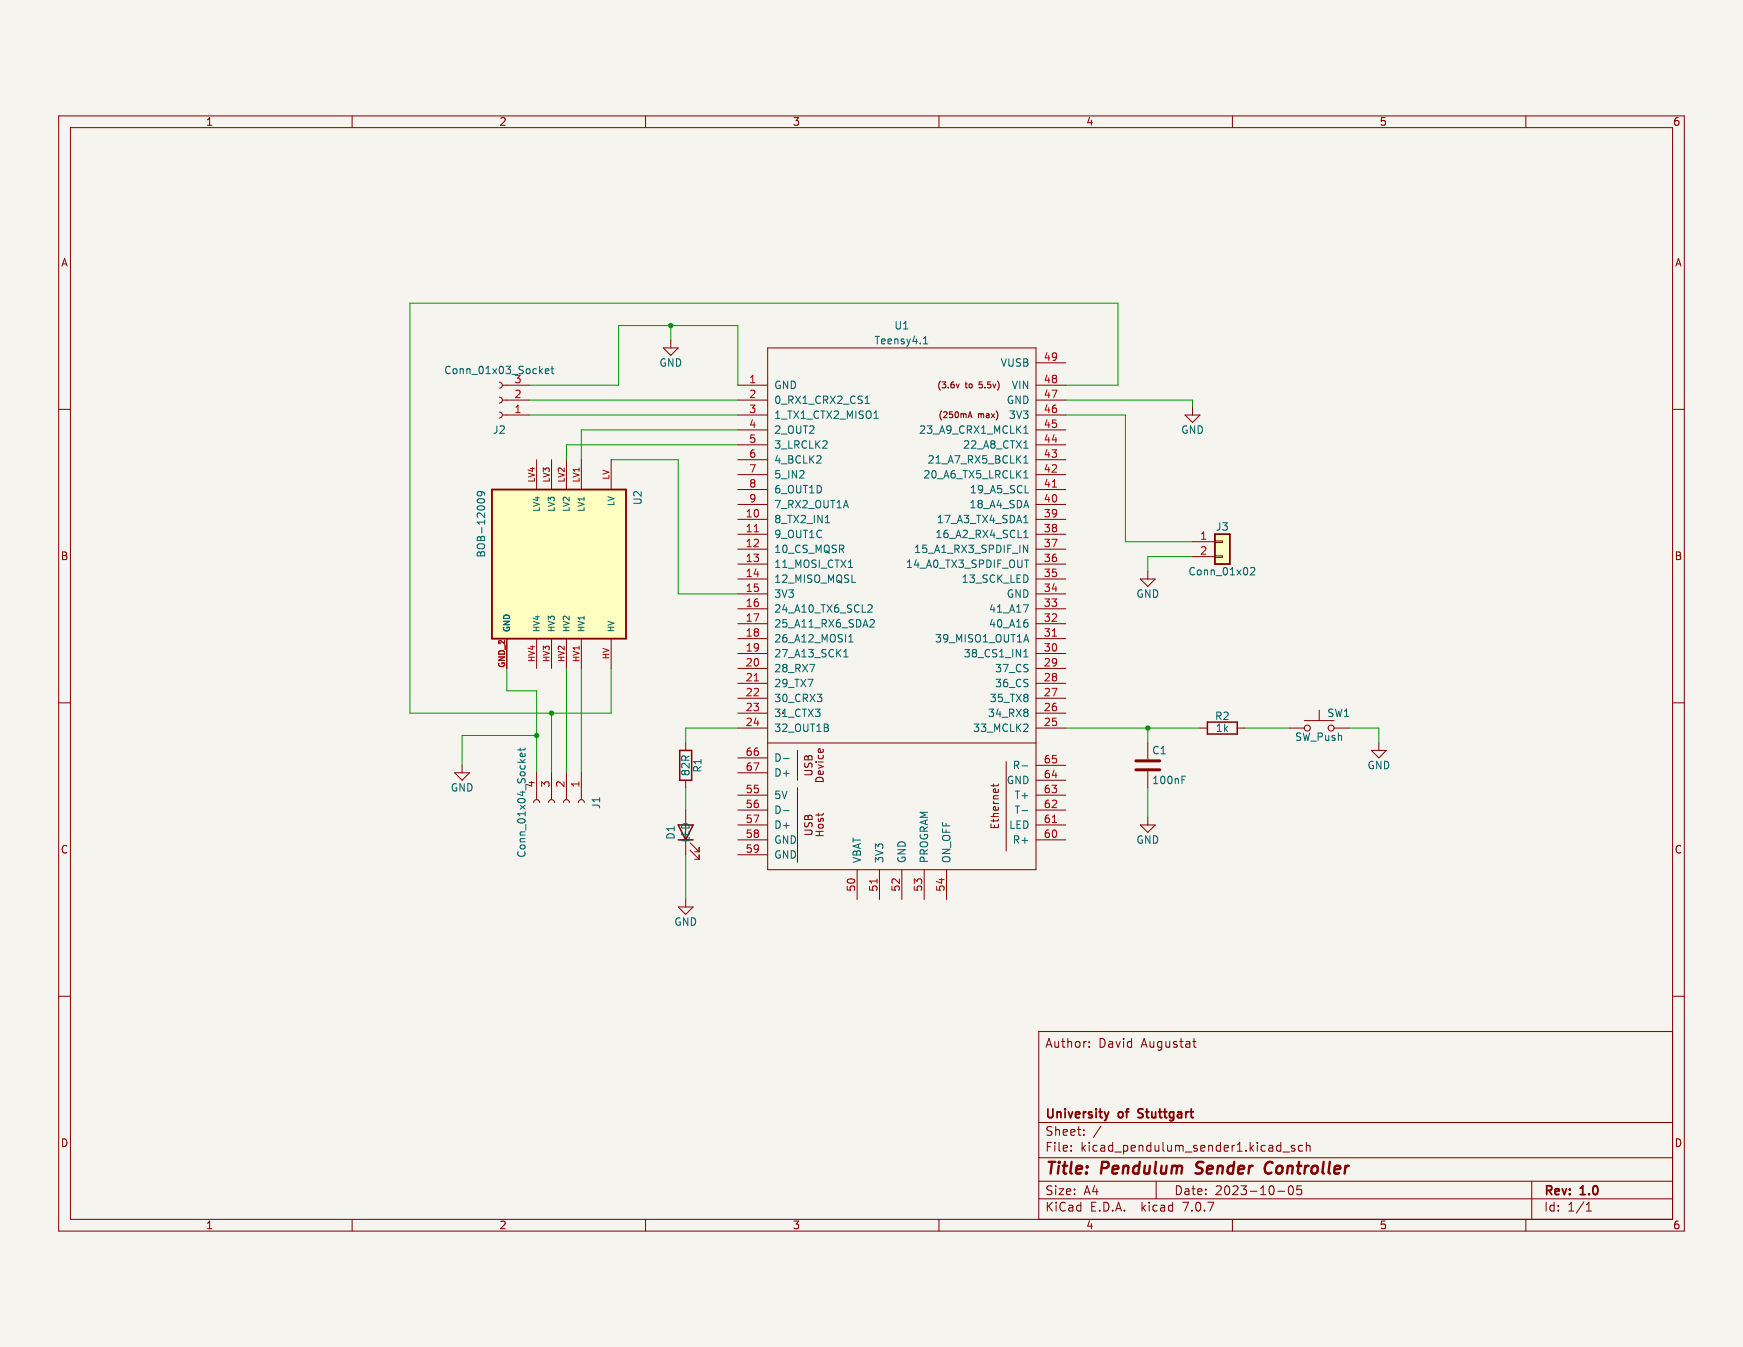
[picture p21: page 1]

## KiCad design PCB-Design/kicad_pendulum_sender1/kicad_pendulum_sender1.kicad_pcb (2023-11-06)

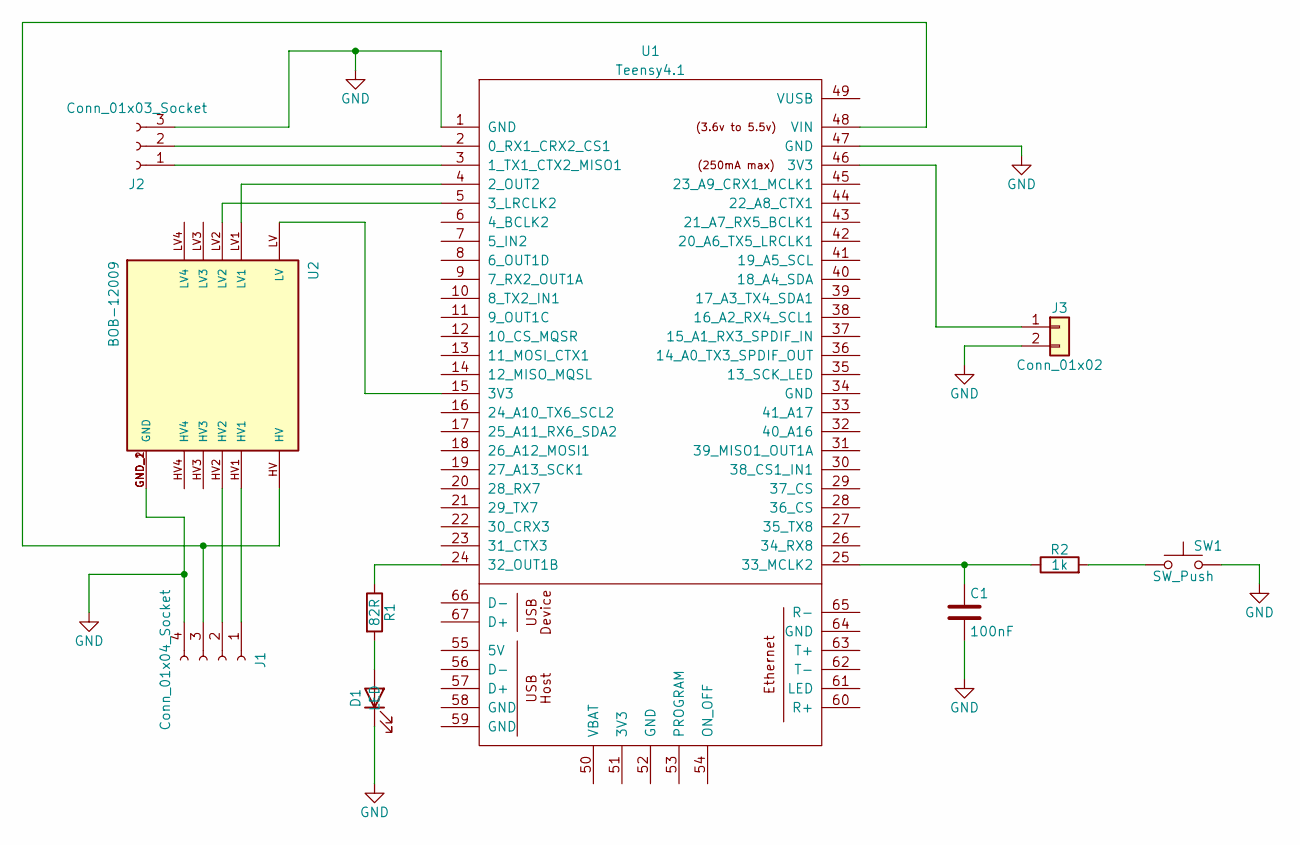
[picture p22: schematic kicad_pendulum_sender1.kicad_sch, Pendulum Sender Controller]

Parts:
C1: 100nF; C_Disc_D4.7mm_W2.5mm_P5.00mm
D1: LED; LED_D3.0mm
J1: Conn_01x04_Socket; TerminalBlock_bornier-4_P5.08mm
J2: Conn_01x03_Socket; TerminalBlock_bornier-3_P5.08mm
J3: Conn_01x02; TerminalBlock_bornier-2_P5.08mm
R1: 82R; R_Axial_DIN0207_L6.3mm_D2.5mm_P10.16mm_Horizontal
R2: 1k; R_Axial_DIN0207_L6.3mm_D2.5mm_P10.16mm_Horizontal
SW1: SW_Push; SW_PUSH_6mm_H5mm
U1: Teensy4.1; Teensy41
U2: BOB-12009; CONV_BOB-12009; PARTREV 01

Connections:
GND: C1.2, D1.1 (K), J1.4, J2.3, J3.2, SW1.2, U1.1 (GND), U1.47 (GND), U2.GND_1 (GND), U2.GND_2 (GND)
unnamed: D1.2 (A), R1.2
unnamed: J1.1, U2.HV1
unnamed: J1.2, U2.HV2
unnamed: J1.3, U1.48 (VIN), U2.HV
unnamed: J2.1, U1.3 (1_TX1_CTX2_MISO1)
unnamed: J2.2, U1.2 (0_RX1_CRX2_CS1)
unnamed: J3.1, U1.46 (3V3)
unnamed: R2.2, SW1.1
unnamed: U1.4 (2_OUT2), U2.LV1
unnamed: U1.15 (3V3), U2.LV
unnamed: U1.5 (3_LRCLK2), U2.LV2
unnamed: R1.1, U1.24 (32_OUT1B)
unnamed: C1.1, R2.1, U1.25 (33_MCLK2)

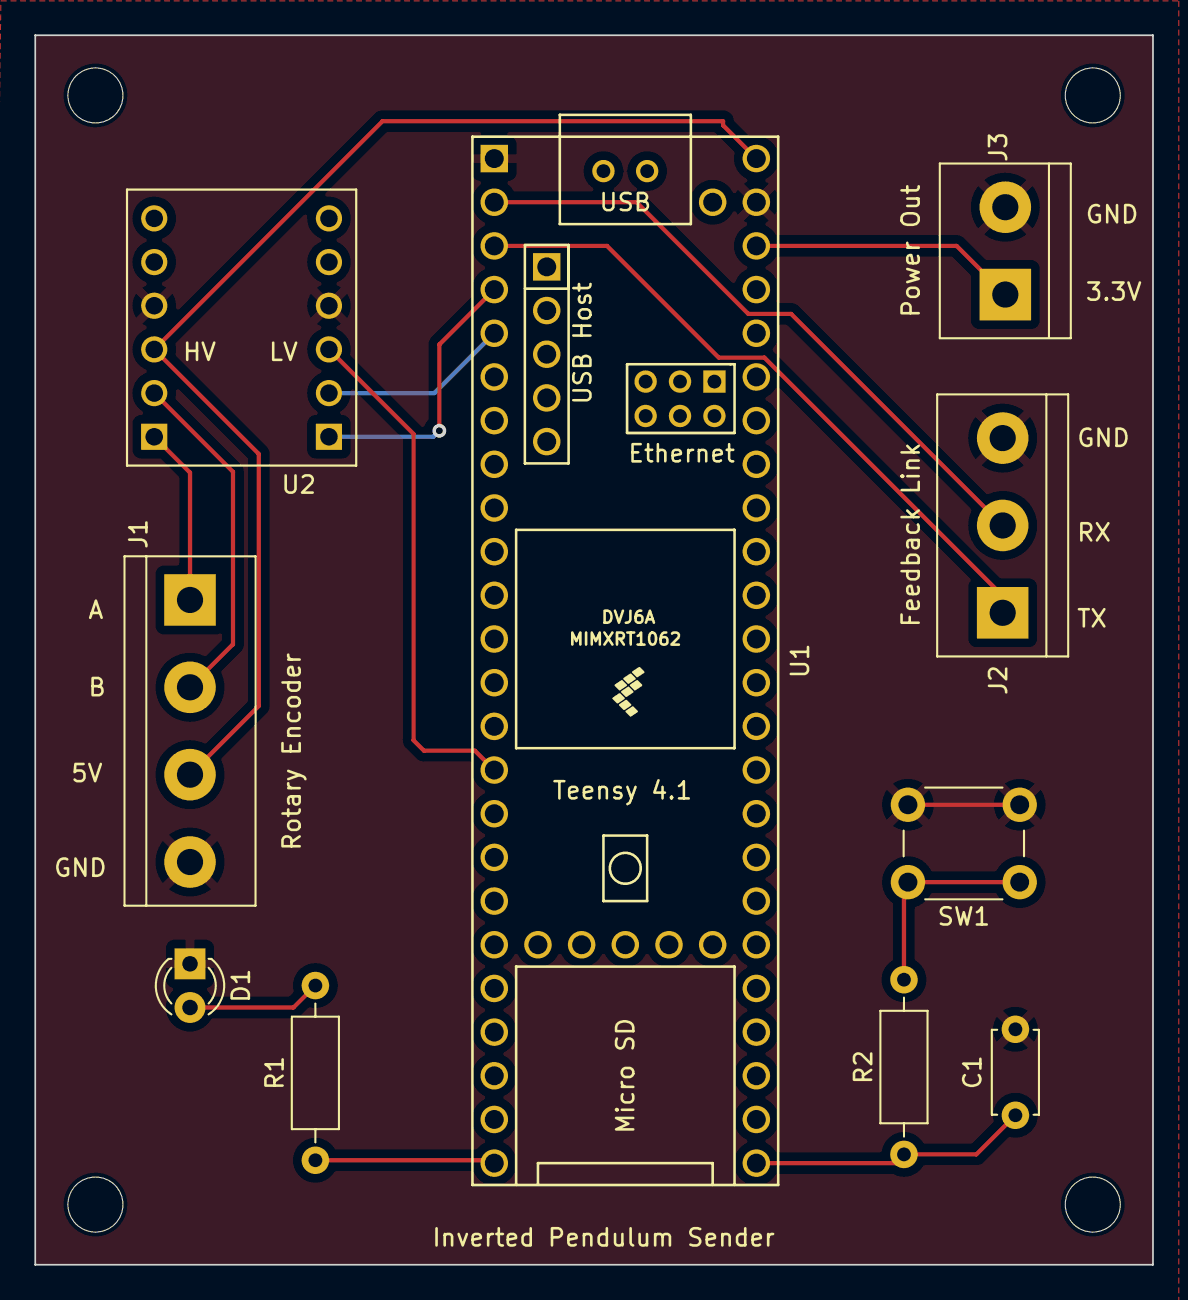
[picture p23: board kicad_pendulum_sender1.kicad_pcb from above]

Board: 2 copper layers, 65.0 x 71.5 mm, 10 parts (0 on the bottom side), 14 nets.

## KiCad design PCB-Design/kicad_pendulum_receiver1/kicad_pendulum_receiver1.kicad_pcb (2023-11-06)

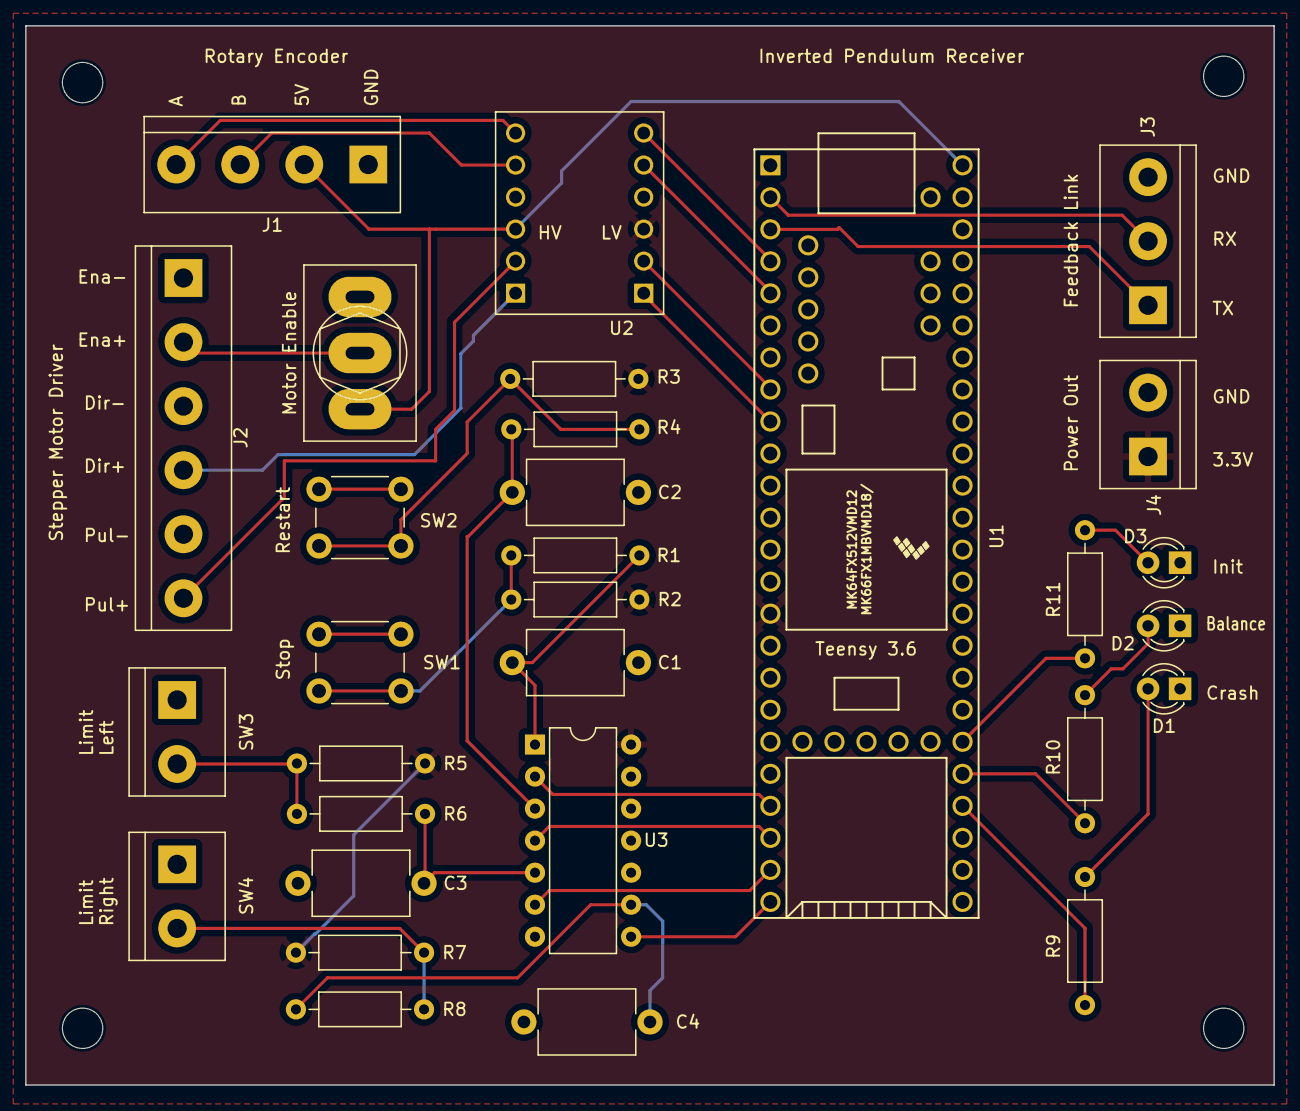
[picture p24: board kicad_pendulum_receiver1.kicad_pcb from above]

Board: 2 copper layers, 99.0 x 84.0 mm, 30 parts (0 on the bottom side), 32 nets.

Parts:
C1, C2, C3, C4: 100nF; C_Disc_D7.5mm_W5.0mm_P10.00mm
D1, D2, D3: LED; LED_D3.0mm
J1: Screw_Terminal_01x04 Enc; TerminalBlock_bornier-4_P5.08mm
J2: Screw_Terminal_01x06 Motor; TerminalBlock_bornier-6_P5.08mm
J3: Screw_Terminal_01x03; TerminalBlock_bornier-3_P5.08mm
J4: Screw_Terminal_01x02; TerminalBlock_bornier-2_P5.08mm
R1, R4, R6, R8: 1k; R_Axial_DIN0207_L6.3mm_D2.5mm_P10.16mm_Horizontal
R2, R3, R5, R7: 10k; R_Axial_DIN0207_L6.3mm_D2.5mm_P10.16mm_Horizontal
R9, R10, R11: 82R; R_Axial_DIN0207_L6.3mm_D2.5mm_P10.16mm_Horizontal
SW1, SW2: SW_Push; SW_PUSH_6mm_H5mm
SW3, SW4: SW_Push; TerminalBlock_bornier-2_P5.08mm
SW5: SW_DPDT_x2; SW_Toggle_Blue_wSlots
U1: Teensy3.6; Teensy35_36
U2: BOB-12009; CONV_BOB-12009
U3: 74HC14; DIP-14_W7.62mm

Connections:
GND: C1.2, C2.2, C3.2, C4.2, D1.1 (K), D2.1 (K), D3.1 (K), J1.1, J2.1, J2.3, J2.5, J3.3, J4.2, SW1.1, SW2.1, SW3.1, SW4.1, SW5.3 (C), U1.1 (GND), U2.GND_1 (GND), U2.GND_2 (GND), U3.7 (GND)
unnamed: C1.1, R1.2, U3.1
unnamed: C2.1, R4.2, U3.3
unnamed: C3.1, R6.2, U3.5
unnamed: C4.1, R8.2, U3.9
unnamed: D1.2 (A), R9.1
unnamed: D2.2 (A), R10.1
unnamed: D3.2 (A), R11.1
unnamed: J1.2, SW5.1 (A), U1.53 (VIN), U2.HV
unnamed: J1.3, U2.HV3
unnamed: J1.4, U2.HV4
unnamed: J2.2, SW5.2 (B)
unnamed: J2.4, U2.HV1
unnamed: J2.6, U2.HV2
unnamed: J3.1, U1.3 (1_TX1_MISO1_TOUCH)
unnamed: J3.2, U1.2 (0_RX1_MOSI1_TOUCH)
unnamed: R1.1, R2.2, SW1.2
unnamed: R3.2, R4.1, SW2.2
unnamed: R5.2, R6.1, SW3.2
unnamed: R7.2, R8.1, SW4.2
unnamed: U1.4 (2_PWM), U2.LV4
unnamed: U1.5 (3_PWM_CAN0TX_SCL2), U2.LV3
unnamed: U1.8 (6_PWM), U2.LV2
unnamed: U1.9 (7_RX3_MISO0_SCL0), U2.LV1
unnamed: U1.21 (29_PWM_CAN0TX_TOUCH), U3.2
unnamed: U1.22 (30_PWM_CAN0RX_TOUCH), U3.4
unnamed: U1.23 (31_A12_RX4_CS1), U3.6
unnamed: U1.24 (32_A13_TX4_SCK1), U3.8
unnamed: R9.2, U1.33 (36_A17_PWM)
unnamed: R10.2, U1.34 (37_A18_PWM_SCL1)
unnamed: R11.2, U1.35 (38_A19_PWM_SDA1)
VCC: J4.1, R2.1, R3.1, R5.1, R7.1, U1.15 (3.3V), U2.LV, U3.14 (VCC)

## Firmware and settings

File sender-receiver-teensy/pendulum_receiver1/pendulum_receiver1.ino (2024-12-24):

#define ENCODER_OPTIMIZE_INTERRUPTS
#include <Encoder.h>
#include <TeensyStep.h>
#include "KalmanAndMLQRParameters.h"

#include <BasicLinearAlgebra.h>

#define FeedbackSerial Serial1

// PINS
constexpr unsigned pinMotorStep = 6;
constexpr unsigned pinMotorDir = 7;
constexpr unsigned pinLimitLeft = 31;
constexpr unsigned pinLimitRight = 32;
constexpr unsigned pinLedRed = 22;
constexpr unsigned pinLedGreen = 23;

// LIBRARY API OBJECTS

// motor controller
Stepper motor(pinMotorStep, pinMotorDir);
RotateControl rotate(5, 1000);
StepControl driveto;

// STEPPER PARAMETERS
constexpr int motorPPR = 1600;
int motorMaxRPM = 20 * 60;  // approx. 1s for track length
int motorPPS = (motorMaxRPM * motorPPR) / 60;
int motorACC = motorPPS * 15;

int homingRPM = motorMaxRPM / 10;  // approx. 10s for track length
float homingFactor = (float)homingRPM / motorMaxRPM;


// DRIVE GEOMETRY

float REV_PER_TRACK = 20.06;
constexpr float trackLengthMeters = 1.2;
float MSTEP_PER_METER = REV_PER_TRACK * motorPPR / trackLengthMeters;
float METER_PER_MSTEP = trackLengthMeters / (REV_PER_TRACK * motorPPR);

float vMaxMeters = METER_PER_MSTEP * motorPPS;
float aMaxMeters = METER_PER_MSTEP * motorACC;

constexpr float safeRangeMeters = 1.0;
constexpr float safePosMeters = safeRangeMeters / 2;
constexpr float safePosPercentage = safePosMeters / trackLengthMeters;

int trackLengthSteps = REV_PER_TRACK * motorPPR;             // initial guess before homing
int safePosSteps = safePosPercentage * trackLengthSteps;     // initial guess
float stepsPerMeter = trackLengthSteps / trackLengthMeters;  // initial guess


// ENCODER PARAMETERS
constexpr int encoderPPRhalf = 600 * 2;
constexpr int encoderPPR = encoderPPRhalf * 2;
constexpr int encoderOrigin = encoderPPRhalf;
constexpr int angleSign = 1;
constexpr float RAD_PER_ESTEP = TWO_PI / encoderPPR;
constexpr float ESTEP_PER_RAD = encoderPPR / TWO_PI;

// Variables for remote encoder input:
int currentEncoderValue = 0;
float currentAngularVelocity = 0;
int currentLatencyMillis = 0;
bool encoderInitialized = false;
bool newEncoderValueAvailable = false;  // set to true after every received value

unsigned long lastSequenceNumber = 0;

// UTILITY FUNCTIONS

int mod(int x, int y) {
  return x < 0 ? ((x + 1) % y) + y - 1 : x % y;
}

int32_t angleSteps(int encoderPos) {
  return angleSign * (mod(encoderPos - encoderOrigin - encoderPPRhalf, encoderPPR) - encoderPPRhalf);
}

float getPoleAngleRad() {  // get encoder angle in radians
  return RAD_PER_ESTEP * angleSteps(currentEncoderValue);
}

float getAngularVelocityRadPerSecond() {
  return currentAngularVelocity;
}

float getCartPosMeter() {
  return METER_PER_MSTEP * motor.getPosition();
}

float getCartSpeedMeter() {  // CAUTION! RotateControl.getCurrentSpeed() only provides step frequency!
  return METER_PER_MSTEP * motor.dir * rotate.getCurrentSpeed();
}


// STATE

enum state { INIT,
             WANDER,
             HOME_LEFT,
             HOME_RIGHT,
             REACH_HOME,
             HOME,
             PERFORM_SWING_UP,
             WAIT_FOR_SWING_UP_SIGNAL,
             BALANCE,
             UNDEFINED } CartState = INIT;
int returnPosition = 0;

unsigned k = 0;

// General and mLQR approach variables:
float xi_cart = 0.0;  // cart position integral [m·s]

float x_cart = 0.0;  // cart position [m]               NOT [msteps]
float v_cart = 0.0;  // cart velocity [m/s]             NOT [msteps/s]
float x_pole = 0.0;  // pole angle [rad]                NOT [esteps]
float v_pole = 0.0;  // pole angluar velocity [rad/s]   NOT [esteps/s]

float poleAngle_p = 0.0;  // previous angle for angular velocity estimation

float u_accel = 0.0;  // previous control input [m/s²]  NOT [msteps/s²]

BLA::Matrix<4, 1> K_iqc = { 13.6723, 13.5022, -74.6153, -19.8637 };

float K_iqc_integrator = 5.0322;

BLA::Matrix<4, 1> x_k;

enum approach {
  MLQR,
  ROBUST_IO
} approachUsed = MLQR;

bool limitLeft;
bool limitRight;


// TIMING

elapsedMillis blinkTimer = 0;  // timer for LED heartbeat
constexpr unsigned blinkPeriod = 250;

elapsedMillis initTimer = 0;  // timer for initial delay
constexpr unsigned initDelay = 2000;

elapsedMillis encoderTimer = 0;  // timer for sending encoder angle over serial
constexpr unsigned encoderPeriod = 2000;

bool isUpright = false;

// CONTROLLER AND FILTER COEFFICIENTS.

unsigned balancePeriod = 50;

float Kxic = 0.25 * Kxc;  // integral gain (TODO: incorporate into system model)

constexpr float f_kf = 0.9;  // factor for complementary filtering of kalman estimate with "raw" measurements


// SAMPLING PERIOD

float Ts = balancePeriod / 1000.0;  // sampling period in seconds
float fs = 1000.0 / balancePeriod;  // sampling frequency in Hz

// Parameters for swing-up:
uint32_t swingUpTimeLastDirSwitch = 0;
int swingUpSampleNMinusOne, swingUpSampleNMinusTwo;
int swingUpDistance = 0.105 * trackLengthSteps;  // with small sail
float swingUpSpeedFactor = 1.0;
float swingUpAccelerationFactor = 1.0;
uint32_t swingUpTimeLastPause = 0;
uint32_t timeBalancingStarted = 0;
const uint32_t balancingGracePeriodMillis = 30000;
bool sendEncoderValuesThroughFeedbackLink = false;
bool doSwingUpAtStart = false;
bool swingUpSignalReceived = false;

bool gracePeriodEnded = false;

void updateParametersForSamplingPeriod(unsigned samplingPeriod) {
  if (samplingPeriod == balancePeriod) {
    return;  // Nothing to do, parameters already set correctly.
  }

  balancePeriod = samplingPeriod;
  Ts = balancePeriod / 1000.0;  // sampling period in seconds
  fs = 1000.0 / balancePeriod;  // sampling frequency in Hz

  updateKalmanAndMLQRParameters(samplingPeriod);
  Kxic = 0.25 * Kxc;  // integral gain (TODO: incorporate into system model)
}

void initializeCartState() {
  CartState = INIT;
  Serial.println("<<< INIT >>>");
  Serial.send_now();
  initTimer = 0;
}

void setApproachFromParameter(int parameter) {
  switch (parameter) {
    case 0: approachUsed = MLQR; break;
    case 1: approachUsed = ROBUST_IO; break;
  }
}

String getUsedApproachString() {
  switch (approachUsed) {
    case MLQR: return "MLQR";
    case ROBUST_IO: return "ROBUST_IO";
  }
  return "";
}

void readInitializationValues() {
  int newMotorMaxRPM;
  float newRevolutionsPerTrack;

  // Expected Format:
  // I:motorMaxRPM;revolutionsPerTrack;doSwingUpAtStart;swingUpDistanceFactor;swingUpSpeedFactor;swingUpAccelerationFactor;K_1;K_2;K_3;K_4;K_integrator;approach\n
  // where doSwingUpAtStart in {0, 1}
  // and approach in {0, 1} with 0: MLQR, 1: ROBUST_IO
  bool receivedInitValues = false;
  while (!receivedInitValues) {
    Serial.println("READY");
    delay(500);

    if (Serial.available() > 0) {
      if (Serial.readStringUntil(':').startsWith("I")) {
        newMotorMaxRPM = Serial.readStringUntil(';').toInt();
        newRevolutionsPerTrack = Serial.readStringUntil(';').toFloat();
        doSwingUpAtStart = Serial.readStringUntil(';').toInt();
        float swingUpDistanceFactor = Serial.readStringUntil(';').toFloat();
        swingUpSpeedFactor = Serial.readStringUntil(';').toFloat();
        swingUpAccelerationFactor = Serial.readStringUntil(';').toFloat();

        K_iqc(0) = Serial.readStringUntil(';').toFloat();
        K_iqc(1) = Serial.readStringUntil(';').toFloat();
        K_iqc(2) = Serial.readStringUntil(';').toFloat();
        K_iqc(3) = Serial.readStringUntil(';').toFloat();
        K_iqc_integrator = Serial.readStringUntil(';').toFloat();
        setApproachFromParameter(Serial.readStringUntil(';').toInt());

        receivedInitValues = true;

        swingUpDistance = swingUpDistanceFactor * trackLengthSteps;

        // Echo received values to computer for validation:
        Serial.printf("Received init values: motor max RPM: %i, revolutions per track: %f, swing up at start: %i, "
                      "swing up distance factor: %f, swing up speed factor %f , swing up accel. factor: %f, "
                      "K_iqc: [%f, %f, %f, %f], K_iqc_integrator: %f, approach: %s\n",
                      newMotorMaxRPM, newRevolutionsPerTrack, doSwingUpAtStart, swingUpDistanceFactor, swingUpSpeedFactor, swingUpAccelerationFactor,
                      K_iqc(0), K_iqc(1), K_iqc(2), K_iqc(3), K_iqc_integrator, getUsedApproachString().c_str());
      }
      Serial.read();  // Remove \n
    }
  }

  updateDriveGeometryParameters(newMotorMaxRPM, newRevolutionsPerTrack);
}

void updateDriveGeometryParameters(int newMotorMaxRPM, float newRevolutionsPerTrack) {
  // STEPPER PARAMETERS
  motorMaxRPM = newMotorMaxRPM;  // approx. 1s for track length
  motorPPS = (motorMaxRPM * motorPPR) / 60;
  motorACC = motorPPS * 15;

  homingRPM = motorMaxRPM / 10;  // approx. 10s for track length
  homingFactor = (float)homingRPM / motorMaxRPM;


  // DRIVE GEOMETRY
  REV_PER_TRACK = newRevolutionsPerTrack;
  MSTEP_PER_METER = REV_PER_TRACK * motorPPR / trackLengthMeters;
  METER_PER_MSTEP = trackLengthMeters / (REV_PER_TRACK * motorPPR);

  vMaxMeters = METER_PER_MSTEP * motorPPS;
  aMaxMeters = METER_PER_MSTEP * motorACC;

  trackLengthSteps = REV_PER_TRACK * motorPPR;           // initial guess before homing
  safePosSteps = safePosPercentage * trackLengthSteps;   // initial guess
  stepsPerMeter = trackLengthSteps / trackLengthMeters;  // initial guess
}

void setup() {
  // set up pins
  pinMode(LED_BUILTIN, OUTPUT);
  pinMode(pinLedRed, OUTPUT);
  pinMode(pinLedGreen, OUTPUT);

#ifdef USE_BOUNCE2
  limitSwitchLeft.attach(pinLimitLeft, INPUT_PULLUP);
  limitSwitchLeft.interval(10);
  limitSwitchRight.attach(pinLimitRight, INPUT_PULLUP);
  limitSwitchRight.interval(10);
#else
  pinMode(pinLimitLeft, INPUT_PULLUP);
  pinMode(pinLimitRight, INPUT_PULLUP);
#endif


  delay(5000);
  Serial.begin(460800);
  Serial.setTimeout(20);

  readInitializationValues();

  FeedbackSerial.begin(115200);
  FeedbackSerial.setTimeout(20);

  motor.setMaxSpeed(motorPPS).setAcceleration(motorACC);
  rotate.rotateAsync(motor);
  rotate.overrideSpeed(0);
  rotate.overrideAcceleration(1.0);

  delay(500);
  Serial.println("Homing and balancing test...");

  limitLeft = digitalRead(pinLimitLeft);
  limitRight = digitalRead(pinLimitRight);

  initializeCartState();
}


void checkLimitSwitches() {
#ifdef USE_BOUNCE2
  if (limitSwitchLeft.update()) {
    limitLeft = limitSwitchLeft.fell();
    digitalWriteFast(pinLedGreen, limitLeft);
    Serial.println(limitLeft ? "Left limit hit!" : "Back on track (from left)");
  }
  if (limitSwitchRight.update()) {
    limitRight = limitSwitchRight.fell();
    digitalWriteFast(pinLedRed, limitRight);
    Serial.println(limitRight ? "Right limit hit!" : "Back on track (from right)");
  }
#else
  bool limitLeftPrev = limitLeft;
  limitLeft = digitalReadFast(pinLimitLeft);
  if (limitLeft != limitLeftPrev) {
    Serial.println(limitLeft ? "Left limit hit!" : "Back on track (from left)");
    digitalWriteFast(pinLedGreen, limitLeft);
  }

  bool limitRightPrev = limitRight;
  limitRight = digitalReadFast(pinLimitRight);
  if (limitRight != limitRightPrev) {
    digitalWriteFast(pinLedRed, limitRight);
    Serial.println(limitRight ? "Right limit hit!" : "Back on track (from right)");
  }
#endif
}
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
void loop() {
  // check limit switches
  checkLimitSwitches();
  updateRotaryEncoderValue();

  // state machine
  switch (CartState) {
    case INIT:  // start wandering unless already at limit...
      if (initTimer >= initDelay) {
        if (limitLeft || limitRight) {
          Serial.println("<<< UNDEFINED >>>");
          Serial.send_now();
          CartState = UNDEFINED;
        } else {
          motor.setPosition(0);
          rotate.overrideSpeed(-homingFactor);  // expect to drive left
          Serial.println("<<< WANDER >>>");
          Serial.send_now();
          CartState = WANDER;
        }
      }
      break;

    case WANDER:  // expect to end up at the left end...
      if (limitLeft) {
        if (limitRight) {
          Serial.println("<<< UNDEFINED >>>");
          Serial.send_now();
          CartState = UNDEFINED;
          break;
        }
        returnPosition = -motor.getPosition();
        motor.setPosition(0);
        // fast return
        rotate.stop();
        motor.setTargetAbs(returnPosition);
        driveto.move(motor);
        // resume homing
        rotate.rotateAsync(motor);
        rotate.overrideSpeed(homingFactor);  // drive right
        Serial.println("<<< HOME RIGHT >>>");
        Serial.send_now();
        CartState = HOME_RIGHT;
      } else if (limitRight) {  // this should not happen in the current setup...
        rotate.stop();
        motor.setInverseRotation(true);  // unexpected direction
        rotate.rotateAsync(motor);
        rotate.overrideSpeed(-homingFactor);  // drive left
        Serial.println("<<< HOME LEFT >>>");
        Serial.send_now();
        CartState = HOME_LEFT;
      }
      break;

    case HOME_LEFT:  // wait for limitLeft (should not happen either, since WANDER will end up at left...)
      if (limitLeft) {
        returnPosition = -motor.getPosition();
        motor.setPosition(0);
        // fast return
        rotate.stop();
        motor.setTargetAbs(returnPosition);
        driveto.move(motor);
        // resume homing
        rotate.rotateAsync(motor);
        rotate.overrideSpeed(homingFactor);  // drive right
        Serial.println("<<< HOME RIGHT >>>");
        Serial.send_now();
        CartState = HOME_RIGHT;
      }
      break;

    case HOME_RIGHT:  // wait for limitRight
      if (limitRight) {
        trackLengthSteps = motor.getPosition();
        rotate.stop();
        safePosSteps = safePosPercentage * trackLengthSteps;
        stepsPerMeter = trackLengthSteps / trackLengthMeters;
        motor.setPosition(trackLengthSteps / 2);
        motor.setTargetAbs(0);
        driveto.move(motor);
        CartState = REACH_HOME;
      }
      break;

    case REACH_HOME:
      Serial.printf("Track length: %d steps = %f m\n", trackLengthSteps, trackLengthMeters);
      Serial.printf("Total revolutions: %f\n", (float)trackLengthSteps / motorPPR);
      Serial.printf("Steps per m: %f\n", stepsPerMeter);
      Serial.printf("Safe range: +/- %d steps = %f m\n", safePosSteps, safePosMeters);
      Serial.printf("Maximum speed: %d steps/s = %f m/s\n", motorPPS, vMaxMeters);
      Serial.printf("Maximum acceleration: %d steps/s² = %f m/s²\n", motorACC, aMaxMeters);
      Serial.printf("Sampling period: %f s\n", Ts);
      Serial.printf("Sampling frequency: %f Hz\n", fs);
      Serial.println("<<< HOME >>>");
      Serial.send_now();
      CartState = HOME;
      break;
    case HOME:  // at home
      if (!doSwingUpAtStart) {
        if (encoderInitialized && encoderTimer >= encoderPeriod) {
          encoderTimer -= encoderPeriod;
          int encoderAbs = currentEncoderValue;
          int encoderRel = angleSteps(encoderAbs);
          bool wasUpright = isUpright;
          isUpright = (abs(encoderRel) < 20);
          if (isUpright && wasUpright) {
            isUpright = false;
            resetControlParameters();
            rotate.rotateAsync(motor);
            rotate.overrideAcceleration(0);
            rotate.overrideSpeed(0);
            Serial.println("<<< BALANCE >>>");
            Serial.send_now();
            CartState = BALANCE;
            timeBalancingStarted = millis();
          } else
            Serial.printf("Encoder_Test: %d -> angle = %d steps = %f°\n", encoderAbs, encoderRel, RAD_TO_DEG * RAD_PER_ESTEP * encoderRel);
          Serial.send_now();
        }
      } else {
        rotate.stop();
        delay(4000);
        resetControlParameters();

        motor.setMaxSpeed((double)motorPPS * swingUpSpeedFactor).setAcceleration((double)motorACC * swingUpAccelerationFactor);

        sendEncoderValuesThroughFeedbackLink = true;
        sendSwingUpStartSignalToSender();
        CartState = PERFORM_SWING_UP;
      }
      break;

    case PERFORM_SWING_UP:
      // Cancel if limit switch gets hit:
      if (limitLeft || limitRight) {
        rotate.overrideAcceleration(1);
        rotate.stop();
        if (limitLeft && limitRight) {
          Serial.println("<<< UNDEFINED >>>");
          CartState = UNDEFINED;
        } else {
          motor.setTargetRel((limitLeft ? 1 : -1) * (int)motorPPR);
          driveto.move(motor);
          initializeCartState();
        }
        break;
      }

      // Swing up:
      if (newEncoderValueAvailable) {
        newEncoderValueAvailable = false;
        ++k;

        int swingUpSampleN = currentEncoderValue;

        // Check if pendulum is upright and then go into balancing mode:
        int upRightThreshold = 40;
        int maxChangeLastTwoSamples = 15;
        if (abs(angleSteps(swingUpSampleN)) < upRightThreshold
            && abs(angleSteps(swingUpSampleNMinusOne)) < upRightThreshold
            && abs(angleSteps(swingUpSampleNMinusTwo)) < upRightThreshold
            && abs(swingUpSampleN - swingUpSampleNMinusOne) + abs(swingUpSampleNMinusOne - swingUpSampleNMinusTwo) < maxChangeLastTwoSamples) {
          Serial.println("Going to balance mode");

          // Restore motor maximum values:
          motor.setMaxSpeed(motorPPS).setAcceleration(motorACC);

          // Initialize parameters and motor for balancing:
          resetControlParameters();
          rotate.rotateAsync(motor);
          rotate.overrideAcceleration(0);
          rotate.overrideSpeed(0);
          Serial.println("<<< BALANCE >>>");
          Serial.send_now();
          timeBalancingStarted = millis();
          CartState = BALANCE;
          break;
        }

        bool isTurningPoint = (swingUpSampleNMinusOne - swingUpSampleNMinusTwo) * (swingUpSampleN - swingUpSampleNMinusOne) <= 0;
        if ((millis() - swingUpTimeLastDirSwitch > 300 && isTurningPoint)) {

          swingUpDistance = -swingUpDistance;  // Change direction of cart

          motor.setTargetAbs(swingUpDistance);
          driveto.move(motor);

          swingUpTimeLastDirSwitch = millis();
        }
        swingUpSampleNMinusTwo = swingUpSampleNMinusOne;
        swingUpSampleNMinusOne = swingUpSampleN;
      }

      // If not successful after certain time, give a pause to restore sync between motor and pendulum movement:
      if (millis() - swingUpTimeLastPause > 15000) {
        Serial.println("Swing-up Pause");
        rotate.overrideAcceleration(0);
        rotate.overrideSpeed(0);
        delay(2000);
        swingUpTimeLastPause = millis();
      }
      break;

    case BALANCE:  // balancing loop
      if (limitLeft || limitRight) {
        rotate.overrideAcceleration(1);
        rotate.stop();
        if (limitLeft && limitRight) {
          Serial.println("<<< UNDEFINED >>>");
          CartState = UNDEFINED;
        } else {
          motor.setTargetRel((limitLeft ? 1 : -1) * (int)motorPPR);
          driveto.move(motor);
          initializeCartState();
        }
        break;
      }

      if (newEncoderValueAvailable) {
        newEncoderValueAvailable = false;
        ++k;

        int32_t cartSteps = motor.getPosition();

        if (abs(cartSteps) >= safePosSteps) {
          rotate.overrideAcceleration(1);
          rotate.stop();
          if (millis() - timeBalancingStarted <= balancingGracePeriodMillis) {
            delay(2000);
            motor.setTargetAbs(0);
            driveto.move(motor);
            Serial.write("Balancing failed within beginning period. Swinging up again.");
            delay(4000);  // Wait for pendulum to loose some energy (overshoots otherwise).
            CartState = HOME;
          } else {
            CartState = WAIT_FOR_SWING_UP_SIGNAL;
            Serial.println("Crashed. Waiting for swing-up signal.");
          }
          break;
        }
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

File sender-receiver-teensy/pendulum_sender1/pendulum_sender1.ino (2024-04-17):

#include <Encoder.h>

#define FeedbackSerial Serial1

constexpr unsigned pinEncoderA = 2;
constexpr unsigned pinEncoderB = 3;
unsigned long transmissionPeriodMillis = 50;
unsigned long sensorPeekPeriodMillis = 10;
constexpr int encoderNumSteps = 2400;

float compareValue = 0;

unsigned long lastTransmissionTime = 0;
unsigned long lastSensorPeekTime = 0;

long sequenceNumber = 1;
long lastReceivedSequenceNumber = 0;
long packetsLostTotal = 0;

enum sendTriggeringApproaches {
  SLIDING_WINDOW,
  SIMPLE_THRESHOLD
} sendTriggeringApproach = SLIDING_WINDOW;

int historySize = 0;
int* samplesHistory;  // Acts as ring buffer
int historyPosition = 0;

// SLIDING_WINDOW:
#define NUM_SAMPLING_PERIODS 10
int samplingPeriodsMillis[NUM_SAMPLING_PERIODS];
float sensitivityFactor = 1.0;
float sensitivityOffset = 0.0;

// SIMPLE_THRESHOLD
float angleTransmissionThreshold; // in degrees
const float simpleThresholdMinDelayBetweenSamples = 50;

double angleSpeed;

Encoder encoder(pinEncoderA, pinEncoderB);
Stream* sensorValueSerial;

void setup() {
  pinMode(LED_BUILTIN, OUTPUT);
  delay(5000);

  Serial.setTimeout(20);

  sensorValueSerial = &Serial;

  readInitializationValues();

  FeedbackSerial.begin(115200);
  FeedbackSerial.setTimeout(20);
}

void readInitializationValues() {
  // Expected Format: 
  // For SLIDING_WINDOW approach:
  // H:0;sensitivityFactor;sensitivityOffset;historySize;period1;period2;period3;period4;period5;period6;period7;period8;period9;period10;\n
  //
  // For SIMPLE_THRESHOLD approach:
  // H:1;angleTransmissionThreshold;\n

  bool receivedHistorySize = false;
  while (!receivedHistorySize) {
    Serial.println("READY");
    delay(500);

    if (Serial.available() > 0) {
      if (Serial.readStringUntil(':').startsWith("H")) {
        int approachInt = Serial.readStringUntil(';').toInt();
        if(approachInt == 0){
          sendTriggeringApproach = SLIDING_WINDOW;
        } else if(approachInt == 1){
          sendTriggeringApproach = SIMPLE_THRESHOLD;
        } else {
          Serial.println("Invalid approach provided");
        }
        if(sendTriggeringApproach == SLIDING_WINDOW){
          sensitivityFactor = Serial.readStringUntil(';').toFloat();
          sensitivityOffset = Serial.readStringUntil(';').toFloat();
          historySize = Serial.readStringUntil(';').toInt();
          for (int i = 0; i < NUM_SAMPLING_PERIODS; i++) {
            samplingPeriodsMillis[i] = Serial.readStringUntil(';').toInt();
          }

          // Echo received values to computer for validation:
          Serial.println("Approach: SLIDING_WINDOW");
          Serial.printf("Received history size: %i\n", historySize);
          Serial.print("Received Sampling Periods: ");
          for (int i = 0; i < NUM_SAMPLING_PERIODS; i++) {
            Serial.printf("%i, ", samplingPeriodsMillis[i]);
          }
          Serial.println();
          Serial.printf("Received sensitivity factor:%f, offset: %f\n", sensitivityFactor, sensitivityOffset);
        } else if(sendTriggeringApproach == SIMPLE_THRESHOLD){
          angleTransmissionThreshold = Serial.readStringUntil(';').toFloat();
          historySize = 2; // needed for angular velocity calculation

          Serial.println("Approach: SIMPLE_THRESHOLD");
          Serial.printf("Received threshold: %f°\n", angleTransmissionThreshold);
        }
      }
      Serial.read();  // Remove \n

      samplesHistory = new int[historySize];
      receivedHistorySize = true;
    }
  }
}

void loop() {
  updateHistoryAndSamplingPeriod();
  switch(sendTriggeringApproach){
    case SLIDING_WINDOW:
      sendSampleIfDelayOver();
      break;
    case SIMPLE_THRESHOLD:
      sendSampleIfAngleThresholdExceeded();
      break;
  }
  checkAndHandleFeedback();
}

void updateHistoryAndSamplingPeriod() {
  unsigned long currentTime = millis();
  if (lastSensorPeekTime + sensorPeekPeriodMillis <= currentTime) {
    int currentEncoderValue = encoder.read();
    lastSensorPeekTime = currentTime;

    // if(sendTriggeringApproach == SLIDING_WINDOW){
    //   compareValue = getHistoryMaxChangeOfCurrent(currentEncoderValue);
    // }

    samplesHistory[historyPosition] = currentEncoderValue;
    historyPosition = (historyPosition + 1) % historySize;

    if(sendTriggeringApproach == SLIDING_WINDOW){
      compareValue = getHistoryMaxChange();

      if (compareValue <= 1.0 * sensitivityFactor + sensitivityOffset) {
        transmissionPeriodMillis = samplingPeriodsMillis[0];
      } else if (compareValue <= 2.0 * sensitivityFactor + sensitivityOffset) {
        transmissionPeriodMillis = samplingPeriodsMillis[1];
      } else if (compareValue <= 3.0 * sensitivityFactor + sensitivityOffset) {
        transmissionPeriodMillis = samplingPeriodsMillis[2];
      } else if (compareValue <= 4.0 * sensitivityFactor + sensitivityOffset) {
        transmissionPeriodMillis = samplingPeriodsMillis[3];
      } else if (compareValue <= 5.0 * sensitivityFactor + sensitivityOffset) {
        transmissionPeriodMillis = samplingPeriodsMillis[4];
      } else if (compareValue <= 6.0 * sensitivityFactor + sensitivityOffset) {
        transmissionPeriodMillis = samplingPeriodsMillis[5];
      } else if (compareValue <= 7.0 * sensitivityFactor + sensitivityOffset) {
        transmissionPeriodMillis = samplingPeriodsMillis[6];
      } else if (compareValue <= 8.0 * sensitivityFactor + sensitivityOffset) {
        transmissionPeriodMillis = samplingPeriodsMillis[7];
      } else if (compareValue <= 9.0 * sensitivityFactor + sensitivityOffset) {
        transmissionPeriodMillis = samplingPeriodsMillis[8];
      } else {
        transmissionPeriodMillis = samplingPeriodsMillis[9];
      }
    }
  }
}

void sendSampleIfDelayOver() {
  unsigned long currentTime = millis();
  if (lastTransmissionTime + transmissionPeriodMillis <= currentTime) {
    sendSample();
  }
}

void sendSampleIfAngleThresholdExceeded(){
  unsigned long currentTime = millis();
  if(lastTransmissionTime + simpleThresholdMinDelayBetweenSamples <= currentTime){
    int encoderValue = encoder.read();
    encoderValue = ((encoderValue % 2400) + 2400) % 2400; // Make sure encoderValue is in [0, 2400)
    const double DEG_PER_ESTEP = 360.0 / 2400.0;
    double poleAngle = DEG_PER_ESTEP * (encoderValue-1200);
    if(abs(poleAngle) >= angleTransmissionThreshold){
      sendSample();
    }
  }
}
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

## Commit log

2022-10-17 Teensy code for Serial via USB approach
2022-10-22 Serial Sensor to Actuator in C++
    Is a bit faster than the Python implementation
2022-10-22 Arduino: Remove balance timer; immediately act when new value received
    Delay between samples is now fully controlled by the sender side.
2022-11-30 Started to implement token bucket
2022-12-02 Token Bucket as CLion Project
2022-12-12 UART serial with adaptive sampling
    Adapting algorithm still needs to be improved. Just a proof of concept until now.
2023-01-04 Implement Multi-threaded Cross Traffic Senders with Logging
2023-01-11 Restructured Logging to make Scheduling Information dynamic
    Before the change all logging classes expected the use of a TokenBucket.
    However, as different scheduling algorithms are to be evaluated, it is
    important that this can be swapped for another scheduling algorithm.
    [PendulumSender.cpp]
2023-01-11 Instantiate PendulumSender and PendulumReceiver in main()
    When instantiated at variable creation (i.e. before main), this led to issues with the CppLinuxSerial library. It complained about the device file not being open.
    [PendulumSender.cpp]
2023-01-12 Fix parsing of pendulum sensor payload in logger
    The samplingPeriodMillis attribute was not parsed from the string correctly.
2023-01-19 Fix output text formatting
    [PendulumSender.cpp]
2023-01-19 Add logging off actuator information
2023-01-19 Arduino Receivers: More machine-readable logging format
    Semicolon-separated values are easier to parse automatically.
2023-01-19 Use unsigned long long to store unix timestamp millis
    Before long was used which caused an overflow on Raspberry Pi 4.
    long is ambiguously defined as 'at least 4 bytes'. Implementation is system-dependent.
    unsigned long long is defined to always have 8 bytes.
2023-01-24 More generic PriorityDeterminer instead of TokenBucket
    This enables swapping out the scheduling mechanism easily.
    [PendulumSender.cpp]
2023-01-25 Extend Linux Receiver to send pause signals to Teensy
    These signals will pause the pendulum for a given amount of milliseconds to
    cause disruption. This decreases the stability of the pendulum which makes the
    tests harder.
    [PendulumReceiver.cpp]
2023-01-25 Extend Teensy Receiver such that it listens for pause signals
2023-01-27 Arduino scripts: Add feedback to sender via serial
2023-01-27 Remove a debug print
2023-01-28 Convert payload size to ethernet frame size before using it for priority determination
2023-01-28 Add scripts to set up scheduling on switch
2023-01-29 PriorityDeterminer: Add reset function
    [PendulumSender.cpp]
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2023-02-02 Switch Scheduling Config: Select predefined parameters via command line arguments
2023-02-02 pendulum_sender1.ino: Restructure sampling period determination
    Now the sampling period is determined by the maximum change between the
    current encoder value and the last 100 encoder values (last second).
    Besides this, the sensor is checked every 10ms regardless of the
    sample transmission period. Thus, the sensor can react faster to
    changes.
2023-02-03 Bugfix in Arduino Sender: Add default value for transmission period
    [pendulum_sender1.ino]
2023-02-07 Use priority 0 data rate as bucket r
    This way it is ensured that the sender stays in priority 0 when it sends with data rate r
2023-02-07 Changed priority and bucket parameters for evaluation
    Both the data-rate to priority mapping and the bucket
    sizes are now more strict.
2023-02-08 Arduino receiver: Parameters for more sampling periods
    These were generated using Ben Carabelli's Julia Script
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2023-03-19 Cmake: Add pthread option
    Otherwise, on some devices compiling of the cross_traffic executable fails
2023-09-07 PendulumSender currentAngle and currentAVG added to output. Teensy Receiver angle calculation simplified.
2023-09-30 Add prioMapping to MultiPriorityTokenBucket class
    I found this code change on the switch PC. Probably it was created by
    Robin.
2023-10-01 Clear serial buffer string before next read.
    This is required due to a change in the CppLinuxSerial library from
    February 2023:
    https://github.com/gbmhunter/CppLinuxSerial/pull/35
    Now, the SerialPort::Read method doesn't overwrite the buffer string
    anymore but appends new input to it.
    [PendulumReceiver.cpp, PendulumSender.cpp]
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2023-10-02 Transmit history size and sampling periods to sender teensy on initialization
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2023-10-04 Read data from receiver config file. Send init parameters to receiver teensy.
2023-10-04 Receiver Teensy: Receive init parameters on startup
    Parameters are read from serial before the actuator starts. This allows for the use of different pendulum types.
    Additionally, I removed the "std::" from "std::abs" as this caused compilation issues.
    [pendulum_receiver1.ino]
2023-10-10 Fix network interface names in configure-switch.sh
2023-10-12 pendulum_receiver1.ino: Replace conversion raw -> degrees -> radians by raw -> radians
    For some unknown reason, the code was altered such that the raw rotary encoder values are first converted into degrees and then this value gets converted into radians (with a bad approximation of Pi).
    Worse than this, a bias in the wrong direction was introduced in the getPoleAngleDeg() method, instead of using the encoderOrigin variable which represents the correct bias.
    I now replaced this by the original implementation, which was correct.
    I also changed the bias from -5 to -10 after experimenting with the new pendulum. Further exploration will show if the bias needs to be parameterized such that it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
    [pendulum_receiver1.ino]
2023-10-20 PendulumSender class: Add callback and method to swap priority determiner
    [PendulumSender.cpp]
2023-10-25 MultiPriorityTokenBucket: Initialize currentSeverityLevel in constructor
    Also added a bounds check in getCostOfCurrentPriority() since there was a segfault that was hard to debug.
2023-10-27 Store Logger as pointer to allow swap without delete
    This is required so that the logger object can be replaced in the PendulumSender and PendulumReceiver while the old logger object is still in progress of saving to file.
    [PendulumReceiver.cpp, PendulumSender.cpp]
2023-10-27 PendulumReceiver.cpp: Access logger as pointer (fix)
    [PendulumReceiver.cpp]
2023-10-27 Bugfix: Print runtime of next config, not current one
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2023-11-03 Damping coefficient for pendulum1_sail10 calculated + bugfix in script. Config files for sequential runs added
    [pendulum1_sail10.csv, pendulum1_sail10_2.csv]
2023-11-06 Teensy Receiver logging every packet, cleaning measurement Python code
2023-11-06 Add KiCAD PCB files
    [BOB-12009.step, Teensy_4.0_Assembly.STEP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]
2023-11-06 pendulum_sender1.ino: Fix Feedback serial packet receiving
    For some reason the feedback packets caused high delays in the sender when used with Teensy 4.1.
    The problem turned out to be the
    FeedbackSerial.readStringUntil(':')
    which blocks the execution until a ':' is found.
    This was now fixed by using non-blocking FeedbackSerial.read() calls.
    [pendulum_sender1.ino]
2023-11-06 No additional newline when printing feedback packet to console
    Feedback packets already contain a '\n'.
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2023-11-15 ReceiverConfig: Print available swing up behaviors on error
2023-11-17 Receiver teensy: Reset control parameters at new config
    [pendulum_receiver1.ino]
2023-11-17 Linux sender/receiver: Reset state on "grace period ended" signal
    [PendulumReceiver.cpp, PendulumSender.cpp]
2023-11-17 Pendulum sender: Change grace period end info print
2023-11-17 Pendulum receiver linux: Search for grace period end signal more generally
    As the buffer might fill during grace period (due to network socket blocking the program execution), we need to search the whole serial buffer for the signal and not just the start of it.
2023-11-17 Init feedback serial link after initialized by PC controller This way the serial connection is established not on plug-in of the USB cable but instead when the sender/receiver linux programs are star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
2023-11-17 Teensy receiver: Use resetControlParameters() method
    [pendulum_receiver1.ino]
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2023-11-17 Teensy receiver: Do not send logs when using Feedback serial for encoder values
    To prevent buffer bloat
    [pendulum_receiver1.ino]
2023-11-17 Teensy receiver: Support for sail type parameters
    Different sails need different parameters for swing-up
2023-11-27 add Kalman Filter comments and update delay in neuerVersuch.m
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2023-11-29 Receiver Teensy: Fix matrix dimensions
    [pendulum_receiver1.ino]
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2023-12-01 Teensy: Transmit angular velocity from sender to receiver
2023-12-01 Change sample size to 64 bytes and move parameters to separate file
2023-12-01 Teensy: Work on new Kalman filter and controller
2023-12-04 fix actuator log for IST approach
    [pendulum_receiver1.ino]
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2023-12-06 Adjust sail parameters for sail14
    The new 3D print is heavier, which gives the system more inertia
2023-12-06 Teensy receiver: accept kalman and controller parameters from serial
2023-12-11 Teensy sender: Parameters for sensitivity factor and offset
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2023-12-11 4th control approach: Fix bug in teensy code
    [pendulum_receiver1.ino]
2024-02-16 Integrate new Carabelli parameters header file into receiver teensy
2024-03-27 Matlab: Print without scientific notation, multiply integrals with B afterwards
    It doesn't matter whether the multiplication with B happens inside the integral or afterwards, but the latter variant is more intuitive
2024-04-09 PendulumSender.cpp: Include network delay in payload (fixed)
    Forgot that there is also an angularVelocity field.
    [PendulumSender.cpp]
2024-04-09 Adapt Arduino code (sender, receiver) to handle latency.
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2024-04-12 Receiver side: Remove pause feature and IST Kalman filter params
2024-04-15 Teensy receiver: Introduce "mLQR" and "RobustIO" instead of internal names.
2024-04-15 Tidy up code, rework some comments
    [PendulumReceiver.cpp]
2024-04-15 Started to implement simpleThreshold approach in Teensy receiver
2024-04-17 Fix bugs in Teensy sender code
    [pendulum_sender1.ino]
2024-12-24 Teensy receiver: Remove non-required using statement
    In the new version of the BasicLinearAlgebra library, this is no longer necessary and even leads to compile errors.
    [pendulum_receiver1.ino]
2024-12-24 Reorganize folders of repository
    [pendulum1_sail10.csv, pendulum1_sail10_2.csv]
2025-01-08 Added 3d printable parts STL + SCAD
    [cable_tower.scad, cable_tower.stl, corner_profile_mount.scad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]

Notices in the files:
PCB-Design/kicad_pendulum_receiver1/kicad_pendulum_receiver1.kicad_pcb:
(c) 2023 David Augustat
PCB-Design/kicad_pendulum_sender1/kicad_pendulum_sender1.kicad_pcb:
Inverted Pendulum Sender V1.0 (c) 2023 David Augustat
